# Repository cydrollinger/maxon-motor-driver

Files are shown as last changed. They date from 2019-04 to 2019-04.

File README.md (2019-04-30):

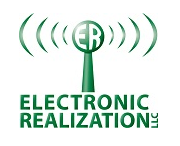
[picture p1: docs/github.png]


>Electronic Realization L.L.C.								   
>Design: Maxon Motor Driver with Bluetooth v4.2/5.0		   
>Engineer: Cy Drollinger								   
>Date: 4/18												           
>Email: cy@elec-real.com
>Website: https://elec-real.com								   
>Address: 2023 Stadium Dr Suite 2B #210 Bozeman, MT 59715				   
>Phone: 406-539-8117	

**NOTE:**
 This case study has been tested and functions as specified. ER is a professional design house and monetary compensation is required for additional work toward this design enabling your monetary success, but conversation is welcome and appreciated toward improving any or all this design and its repository. 

 Think critically while operating and or redesigning this system. Open electronic circuitry can be dangerous due to easily shorting circuits which can generate immediate and intense heat resulting in fire. This is only one example of ill advised use. 			   
	 
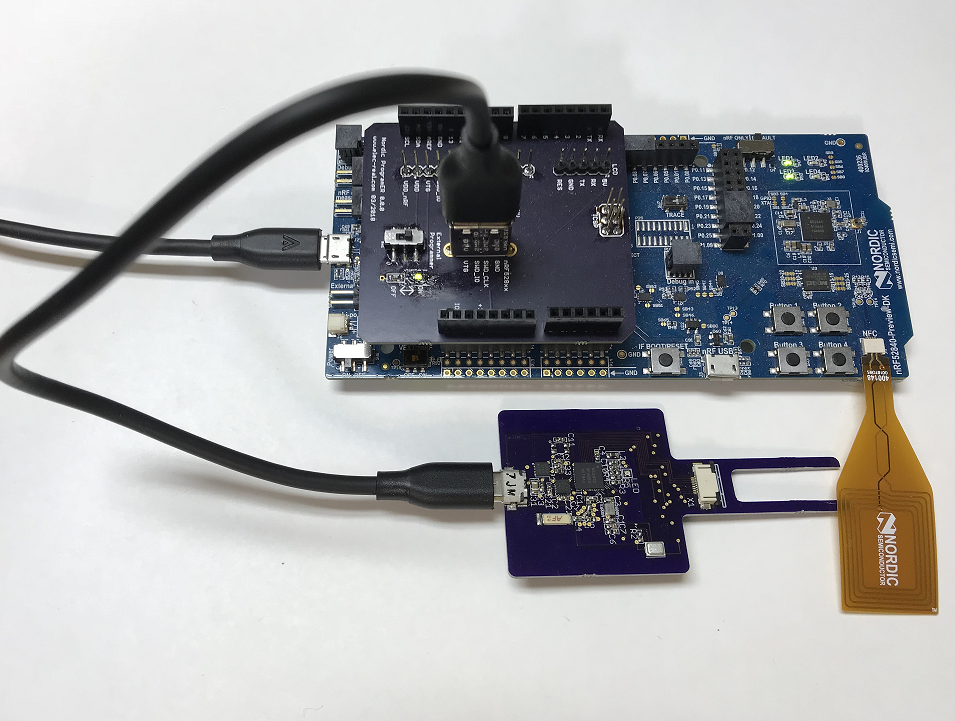
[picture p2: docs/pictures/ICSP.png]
Maxon Motor Driver


**PURPOSE:**
The puspose of this design was to implement a 3 phase DC motor driver for a high speed 8mm dia motor by
Maxon. The system utilizes the nRF52832 by Nordic Semicondutor which outputs bluetooth v4.2/5.0 wireless
communication. The device also boast the mpu9250 a 9 axis inertial sensor as well as a TDK's MEMs micro phone. 

>**File Arcitecture with a terse description**

* FOLDERS:
	* docs		: datasheets charging IC and battery holder
	* hardware	: eagle cadsoft(v7.7) hardware design files 	
		* library		: eagle part files 
		* manufacturing	: files required to produce the design
			* bom	: files created to order the parts	
			* gerber	: files generated to manufacture the board
			* 
	* readme.md	: this file
	
(http://www.youtube.com/watch?v=88ky35AwuC4 "maxon motor driver")

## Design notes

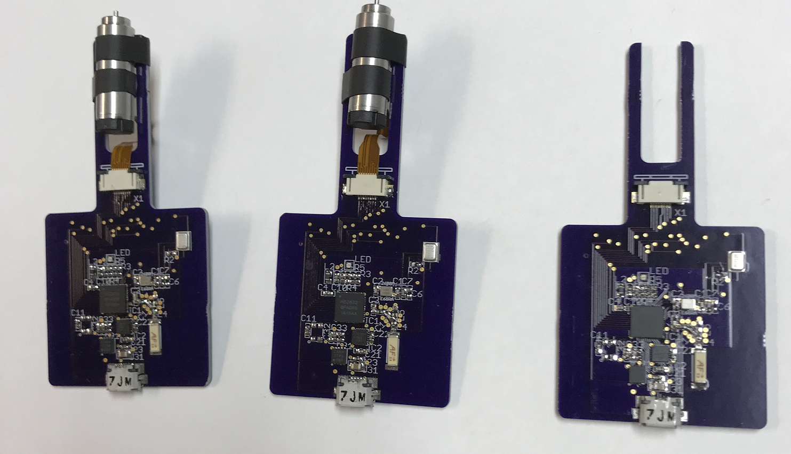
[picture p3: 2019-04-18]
docs/pictures/Max Motor.png

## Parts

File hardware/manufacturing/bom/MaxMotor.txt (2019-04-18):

Partlist exported from C:/Users/Cy/Documents/eagle/Max motor/MaxMotor.sch at 4/23/2018 2:59 PM

Qty Value                       Device                      Package              Parts            Description                                      

1   ANTENNA2SMD5                ANTENNA2SMD5                ANTENNA-CHIP5        U$1              Antenna                                          

CAPACITOR
1   .8pF                        C-ERC0402                   C0402                C3                                                                
1   2.2pF                       C-ERC0402                   C0402                C13                                                               
2   20pF                        C-ERC0402                   C0402                C1, C2                                                            
1   100pF                       C-ERC0402                   C0402                C7                                                                
1   1.0nF                       C-ERC0402                   C0402                C32                                                               
1   10nF                        C-ERC0402                   C0402                C22                                                               
3   100nF                       C-ERC0402                   C0402                C4, C5, C8, C11, C21, C23                                                        
2   1.0uF                       C-ERC0402                   C0402                C10, C33                                                          
2   4.7UF                       C-ER                        C0805                C9, C31                                                               
1                               C-ERC0402                   C0402                C6                                                                

CONNECTOR
1   MICRO-USB-SHIELD-ZX62R-B-5P MICRO-USB-SHIELD-ZX62R-B-5P ZX62R-B-5P           U$4              Hirose Micro USB Connector                       
1   52745-0890                  52745-0890                  52745-0890           X1               FFC/FPC-to-Board  0.50mm (.020") SMT Top Contact 

CRYSTAL
1   FA-128                      FA-128                      FA-128               16M                                                               

IC
1   NRF52832                    NRF52832                    QFN48                IC1                                                               
1   MPU9250_CORRECTED           MPU9250_CORRECTED           3X3_24_QFN_CORRECTED IC2                                                               
1   MCP1727                     MCP1727                     DFN8-3X3             IC3                                                               
1   TSL238T                     TSL238T                     T4                   IC4                                                               
2   ICS-43432                   Microphone                  ICS-43432            IC5, IC6

INDUCTOR
2   3.9nH                       L-ERL402                    R0402                L1, L4                                                            
1   15nH                        L-ERL402                    R0402                L3                                                                
1   10UH                        L-ERL603                    R0603                L2                                                                
1   N.C.                        L-ERL402                    R0402                L5                                                                

LED
1   1X1RGB                      1X1RGB                      1X1                  LED                                                               

RESISTOR
1   0                           R-ER-TINYR402               R0402                R1                                                                
4   100                         R-ER-TINYR402               R0402                R3, R4, R5, R31                                                   
1   100k                        R-ERR0402                   R0402                R2                                                                

TRANSISTOR
3   FDC2512                     FDC2512                     SSOT6                MD12, MD22, MD32                                                  
3   NCP45524/25                 NCP45524/25                 DFN8                 U$2, U$5, U$6

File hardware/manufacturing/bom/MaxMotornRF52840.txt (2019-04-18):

Partlist exported from C:/Users/Cy/Documents/eagle/Max motor/MaxMotornRF52840.sch at 2/5/2019 1:46 PM

Qty Value        Device                      Package              Parts                  Description                                      DIGIKEY     
ANTENNA
1   ANTENNA2SMD5 ANTENNA2SMD5                ANTENNA-CHIP5        ANT1                   Antenna                                                      

CAPACITORS
2   1.0pF        C-ER201                     C0201                C3, C4                                                                              
2   12pF         C-ER201                     C0201                C1, C2                                                                              
2   20pF         C-ER201                     C0201                C17, C18                                                                            
1   100pF        C-ER201                     C0201                C5                                                                                  
1   820pF        C-ER201                     C0201                C9                                                                                  
2   1.0nF        C-ER201                     C0201                C32, C72                                                                            
4   100nF        C-ER201                     C0201                C7, C8, C10, C12                                                                    
4   1.0uF        C-ER201                     C0201                C33, C73, C14, C15                                                                            
6   4.7uF        C-ERC0402                   C0402                C6, C19, C20, C25,C31, C71                                                                   
3   N.C.         C-ER201                     C0201                C13, C16, C24                                                                       
3                C-ER201                     C0201                C21, C22, C23                                                                       

CLOCK
1   ABM12        ABM12                       ABM12                X2                                                                      SER3800CT-ND
1   ECX32        ECX32                       ECX39                X3                                                                                  

CONNECTOR
1   52745-0890   52745-0890                  52745-0890           X1                     FFC/FPC-to-Board  0.50mm (.020") SMT Top Contact             
1   usb          MICRO-USB-SHIELD-ZX62R-B-5P ZX62R-B-5P           USB/SWD                Hirose Micro USB Connector                                   

DIODE
1                DIODE-SOD123                SOD123               D1                     DIODE                                                        

INDUCTOR
1   3.9nH        L-ER0201                    C0201@1              L1                                                                                  

INTEGRATED CIRCUIT
1   NRF52840     NRF52840                    AQFN73               IC1                                                                                 
1   ICM20948     ICM20948                    3X3_24_QFN_CORRECTED IC2                                                                                 
2   MCP1727      MCP1727                     DFN8-3X3             IC3, IC7                                                                            
2   ICS-43432    ICS-43432                   ICS-43432            IC5, IC6                                                                            

LED
1   1X1RGB       1X1RGB                      1X1                  LED                                                                                 

RSISTOR
1   0            R-ER-TINY                   R0805                R1                                                                                  
4   0            R-ER0201                    R0201                R6, R7, R8, R9                                                                      
5   100          R-ER0201                    R0201                R3, R4, R5, R31, R71                                                                
3   10k          R-ER0201                    R0201                R10, R11, R12                                                                       
1   100k         R-ER0201                    R0201                R2                                                                                  

TRANSISTOR
6   DMN2320      DMN2320                     AP02002              M1, M2, M3, M4, M5, M6                                                              
3   NCP45524/25  NCP45524/25                 DFN8                 M7, M8, M9

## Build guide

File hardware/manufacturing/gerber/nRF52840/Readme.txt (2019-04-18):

TOP LAYER
top.GTL
topsilk.GTO
topstop.GTS
toppaste.gtp

SECOND LAYER
layer2.G2L

THIRD LAYER
layer3.G3L

BOTTOM LAYER
botsilk.GBO
botstop.GBS
bottom.GBL
botpaste.gbp

HOLES
holes.xln

BOARD OUTLINE
board_ouline.GKO 		//approximately 1.5" x 3.0" 

INSTRUCTIONS
The microstrip is based on calculations from High-Speed Digital Design pg 430

	height: .0067 in.
	width: .014 in.
	er:    3.66
        thickness: .00138

Color: mask Blue silk Yellow

Surface finish: ENEPIG
Board thickness standard ~0.063"

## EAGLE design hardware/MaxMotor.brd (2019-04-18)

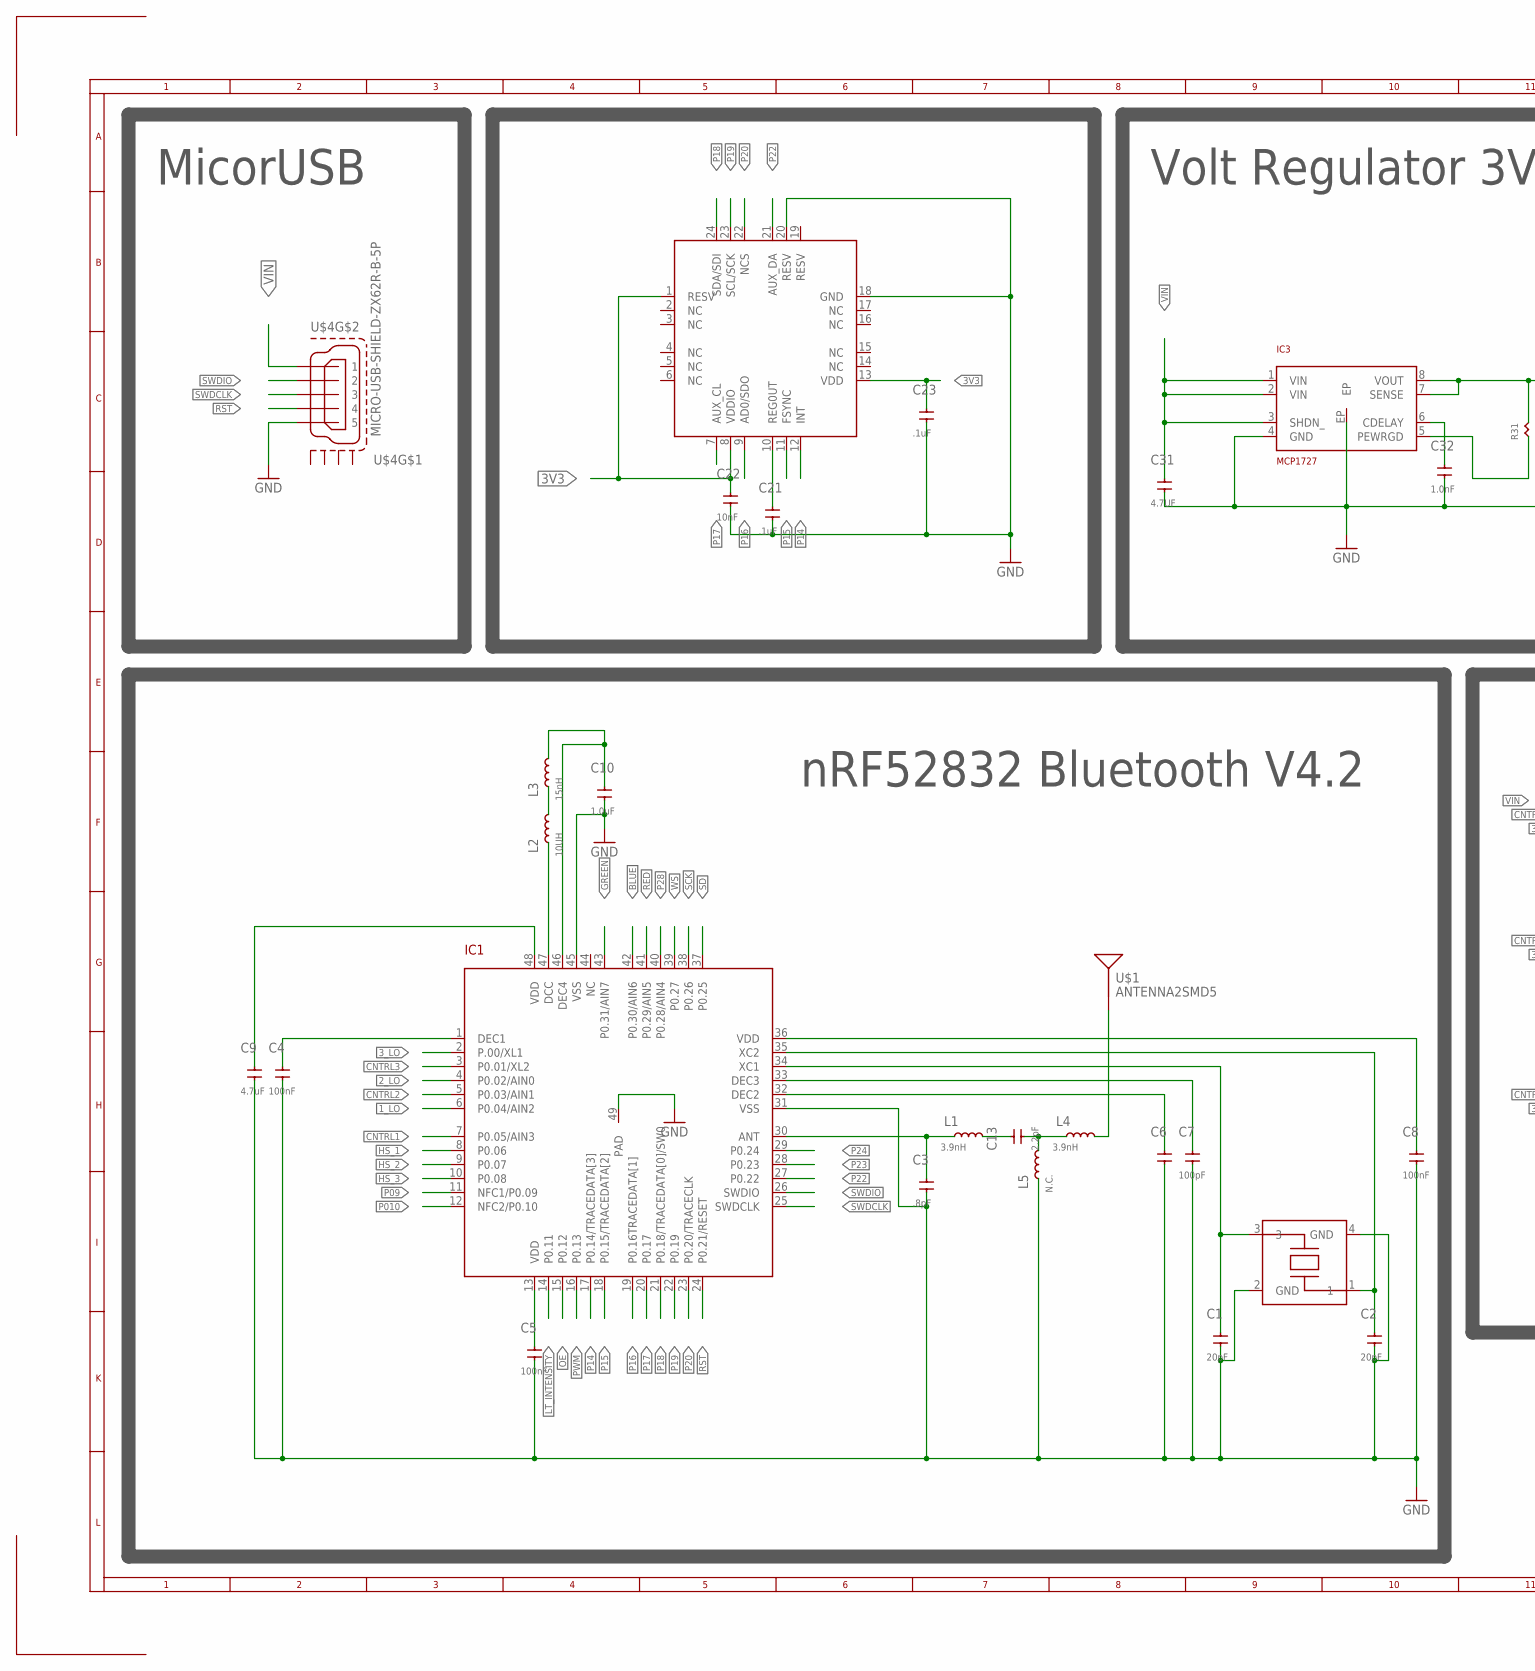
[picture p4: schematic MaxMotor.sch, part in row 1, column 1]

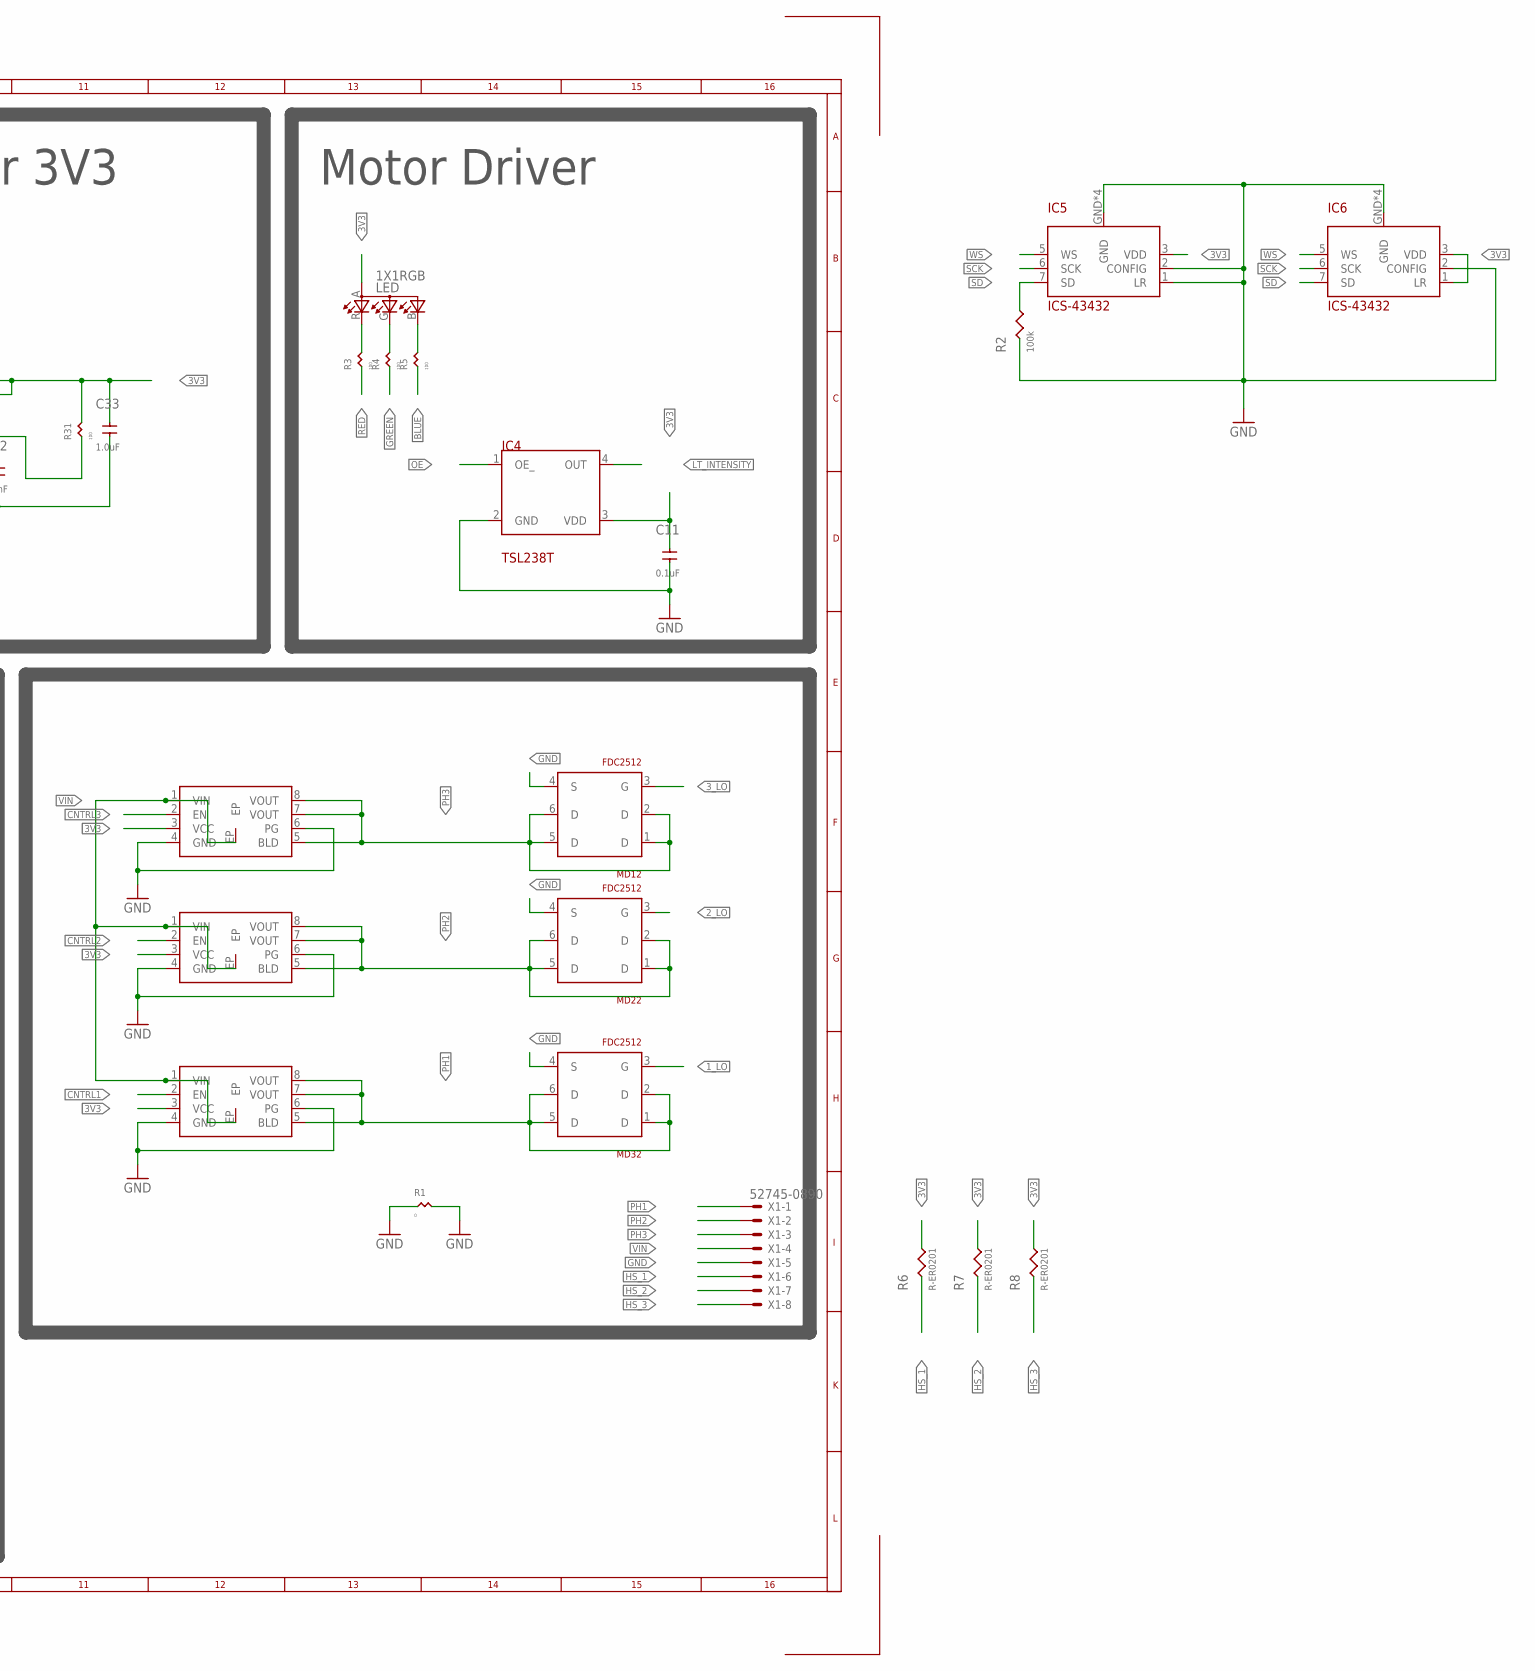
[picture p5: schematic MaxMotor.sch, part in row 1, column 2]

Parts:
C1, C2: 20pF; C0402
C3: .8pF; C0402
C4, C5, C8: 100nF; C0402
C6: C-ERC0402; C0402
C7: 100pF; C0402
C9: 4.7uF; C0805
C10, C33: 1.0uF; C0402
C11: 0.1uF; C0402
C13: 2.2pF; C0402
C21, C23: .1uF; C0402
C22: 10nF; C0402
C31: 4.7UF; C0805
C32: 1.0nF; C0402
IC1: NRF52832; QFN48
IC2: MPU9250_CORRECTED; 3X3_24_QFN_CORRECTED
IC3: MCP1727; DFN8-3X3
IC4: TSL238T; T4
IC5, IC6: ICS-43432
L1, L4: 3.9nH; R0402
L2: 10UH; R0603
L3: 15nH; R0402
L5: N.C.; R0402
LED: 1X1RGB; 1X1
MD12, MD22, MD32: FDC2512; SSOT6
R1: 0; R0402
R2: 100k; R0402
R3, R4, R5, R31: 100; R0402
R6, R7, R8: R-ER0201; R0201
U$1: ANTENNA2SMD5; ANTENNA-CHIP5
U$2, U$5, U$6: NCP45524/25; DFN8
U$4: MICRO-USB-SHIELD-ZX62R-B-5P; ZX62R-B-5P
X1: 52745-0890
XTL16M: FA-128

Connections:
1_LO: IC1.6 (P0.04/AIN2), MD32.3 (G)
2_LO: IC1.4 (P0.02/AIN0), MD22.3 (G)
3V3: C5.2, C8.2, C9.2, C11.2, C22.2, C23.2, C33.2, IC1.13 (VDD), IC1.36 (VDD), IC1.48 (VDD), IC2.1 (RESV), IC2.8 (VDDIO), IC2.13 (VDD), IC3.7 (SENSE), IC3.8 (VOUT), IC4.3 (VDD), IC5.3 (VDD), IC6.1 (LR), IC6.3 (VDD), LED.A (A2), R6.2, R7.2, R8.2, R31.2, U$2.3 (VCC), U$5.3 (VCC), U$6.3 (VCC)
3_LO: IC1.2 (P.00/XL1), MD12.3 (G)
BLUE: IC1.42 (P0.30/AIN6), R5.1
CNTRL1: IC1.7 (P0.05/AIN3), U$6.2 (EN)
CNTRL2: IC1.5 (P0.03/AIN1), U$5.2 (EN)
CNTRL3: IC1.3 (P0.01/XL2), U$2.2 (EN)
GND: C1.1, C2.1, C3.1, C4.1, C5.1, C6.1, C7.1, C8.1, C9.1, C10.1, C11.1, C21.1, C22.1, C23.1, C31.1, C32.1, C33.1, IC1.31 (VSS), IC1.45 (VSS), IC1.49 (PAD), IC2.18 (GND), IC2.20 (RESV), IC3.4 (GND), IC3.EP, IC4.2 (GND), IC5.1 (LR), IC5.2 (CONFIG), IC5.GND, IC5.GND@ (GND), IC5.GND@1 (GND), IC5.GND@2 (GND), IC6.2 (CONFIG), IC6.GND, IC6.GND@ (GND), IC6.GND@1 (GND), IC6.GND@2 (GND), L5.1, MD12.4 (S), MD22.4 (S), MD32.4 (S), R1.1, R1.2, R2.1, U$2.4 (GND), U$2.6 (PG), U$4.1 (5), U$5.4 (GND), U$5.6 (PG), U$6.4 (GND), U$6.6 (PG), X1.5, XTL16M.2 (GND), XTL16M.4 (GND)
GREEN: IC1.43 (P0.31/AIN7), R4.1
HS_1: IC1.8 (P0.06), R6.1, X1.6
HS_2: IC1.9 (P0.07), R7.1, X1.7
HS_3: IC1.10 (P0.08), R8.1, X1.8
LT_INTENSITY: IC1.14 (P0.11), IC4.4 (OUT)
unnamed: C21.2, IC2.10 (REG0UT)
unnamed: C3.2, IC1.30 (ANT), L1.1
unnamed: C6.2, IC1.32 (DEC2)
unnamed: C13.2, L1.2
unnamed: C7.2, IC1.33 (DEC3)
unnamed: C1.2, IC1.34 (XC1), XTL16M.3
unnamed: C2.2, IC1.35 (XC2), XTL16M.1
unnamed: IC1.47 (DCC), L2.1
unnamed: L2.2, L3.1
unnamed: C10.2, IC1.46 (DEC4), L3.2
unnamed: LED.B (CGREEN), R5.2
unnamed: C13.1, L4.1, L5.2
unnamed: L4.2, U$1.FEED
unnamed: LED.G (CBLUE), R4.2
unnamed: IC3.5 (PEWRGD), R31.1
unnamed: LED.R (CRED), R3.2
unnamed: C32.2, IC3.6 (CDELAY)
unnamed: C4.2, IC1.1 (DEC1)
OE: IC1.15 (P0.12), IC4.1 (OE_)
P09: IC1.11 (NFC1/P0.09)
P010: IC1.12 (NFC2/P0.10)
P14: IC1.17 (P0.14/TRACEDATA[3]), IC2.12 (INT)
P15: IC1.18 (P0.15/TRACEDATA[2]), IC2.11 (FSYNC)
P16: IC1.19 (P0.16TRACEDATA[1]), IC2.9 (AD0/SDO)
P17: IC1.20 (P0.17), IC2.7 (AUX_CL)
P18: IC1.21 (P0.18/TRACEDATA[0]/SW0), IC2.24 (SDA/SDI)
P19: IC1.22 (P0.19), IC2.23 (SCL/SCK)
P20: IC1.23 (P0.20/TRACECLK), IC2.22 (NCS)
P22: IC1.27 (P0.22), IC2.21 (AUX_DA)
P23: IC1.28 (P0.23)
P24: IC1.29 (P0.24)
P28: IC1.40 (P0.28/AIN4)
PH1: MD32.1 (D), MD32.2 (D), MD32.5 (D), MD32.6 (D), U$6.5 (BLD), U$6.7 (VOUT), U$6.8 (VOUT), X1.1
PH2: MD22.1 (D), MD22.2 (D), MD22.5 (D), MD22.6 (D), U$5.5 (BLD), U$5.7 (VOUT), U$5.8 (VOUT), X1.2
PH3: MD12.1 (D), MD12.2 (D), MD12.5 (D), MD12.6 (D), U$2.5 (BLD), U$2.7 (VOUT), U$2.8 (VOUT), X1.3
PWM: IC1.16 (P0.13)
RED: IC1.41 (P0.29/AIN5), R3.1
RST: IC1.24 (P0.21/RESET), U$4.2 (4)
SCK: IC1.38 (P0.26), IC5.6 (SCK), IC6.6 (SCK)
SD: IC1.37 (P0.25), IC5.7 (SD), IC6.7 (SD), R2.2
SWDCLK: IC1.25 (SWDCLK), U$4.3
SWDIO: IC1.26 (SWDIO), U$4.4 (2)
VIN: C31.2, IC3.1 (VIN), IC3.2 (VIN), IC3.3 (SHDN_), U$2.1 (VIN), U$2.EP, U$4.5 (1), U$5.1 (VIN), U$5.EP, U$6.1 (VIN), U$6.EP, X1.4
WS: IC1.39 (P0.27), IC5.5 (WS), IC6.5 (WS)

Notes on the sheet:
nRF52832 Bluetooth V4.2
MicorUSB
Volt Regulator 3V3
Motor Driver

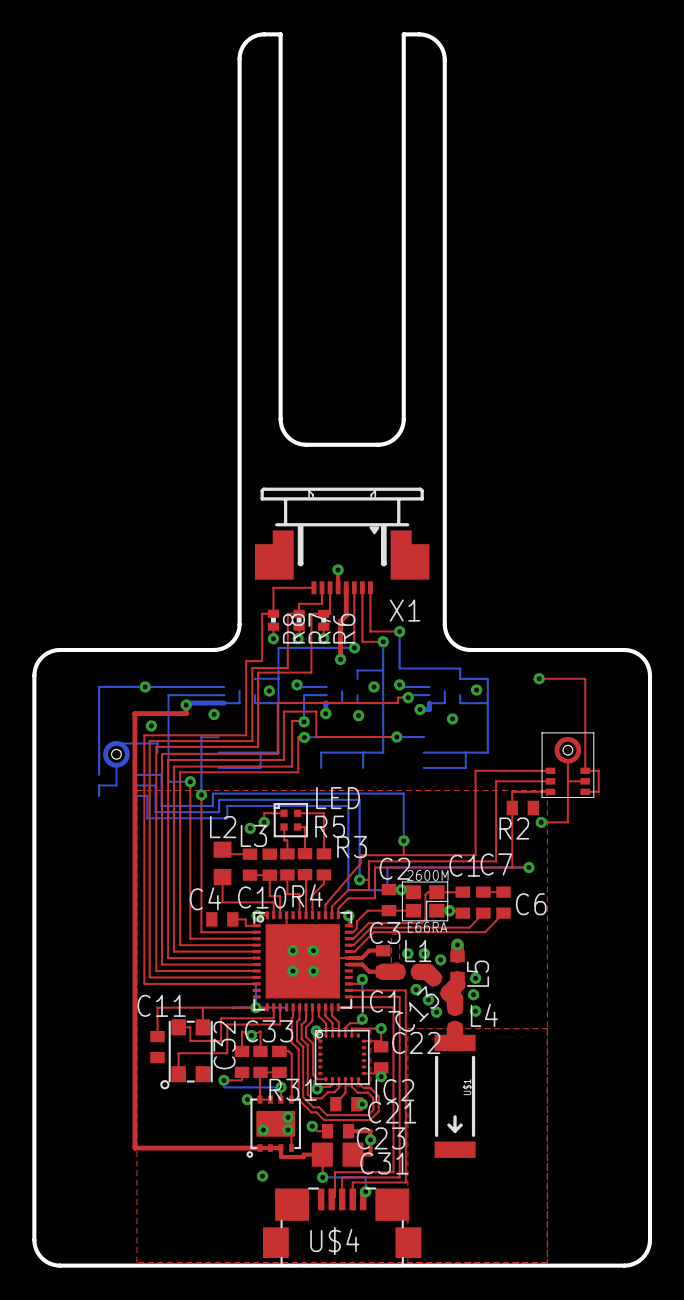
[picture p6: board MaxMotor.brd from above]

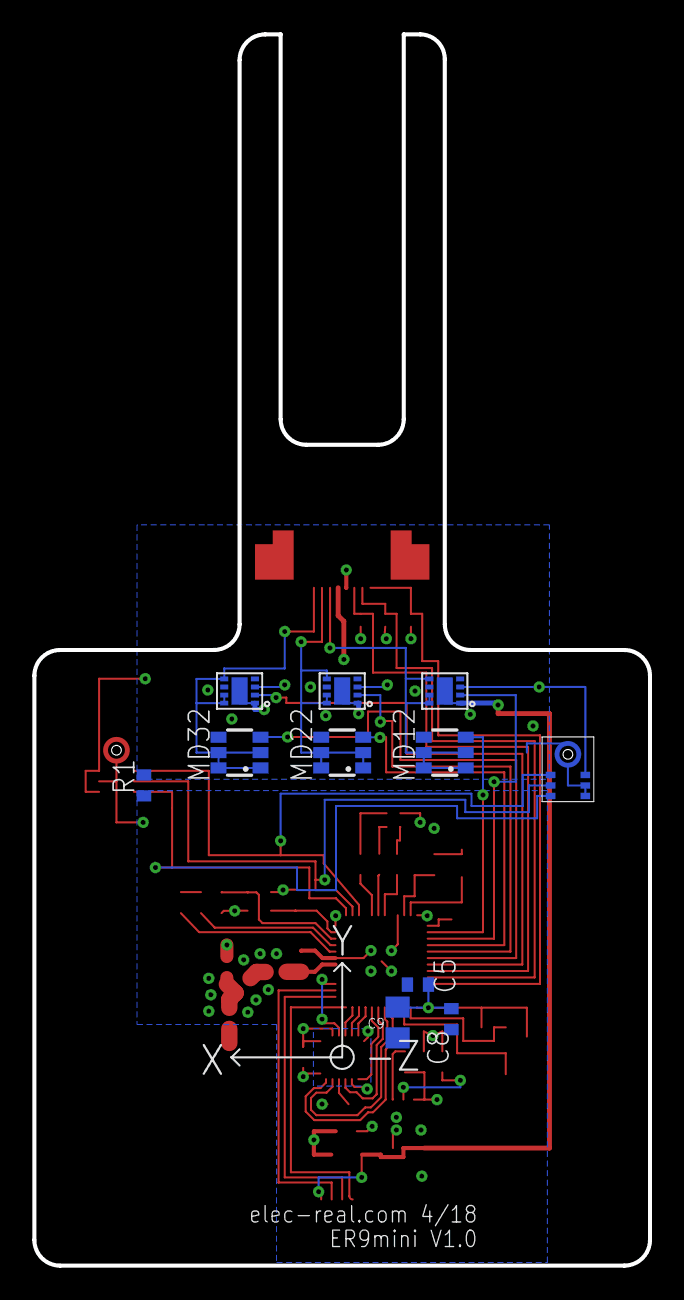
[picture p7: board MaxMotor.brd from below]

Board: 4 copper layers, 38.1 x 76.2 mm, 49 parts (11 on the bottom side), 52 nets.

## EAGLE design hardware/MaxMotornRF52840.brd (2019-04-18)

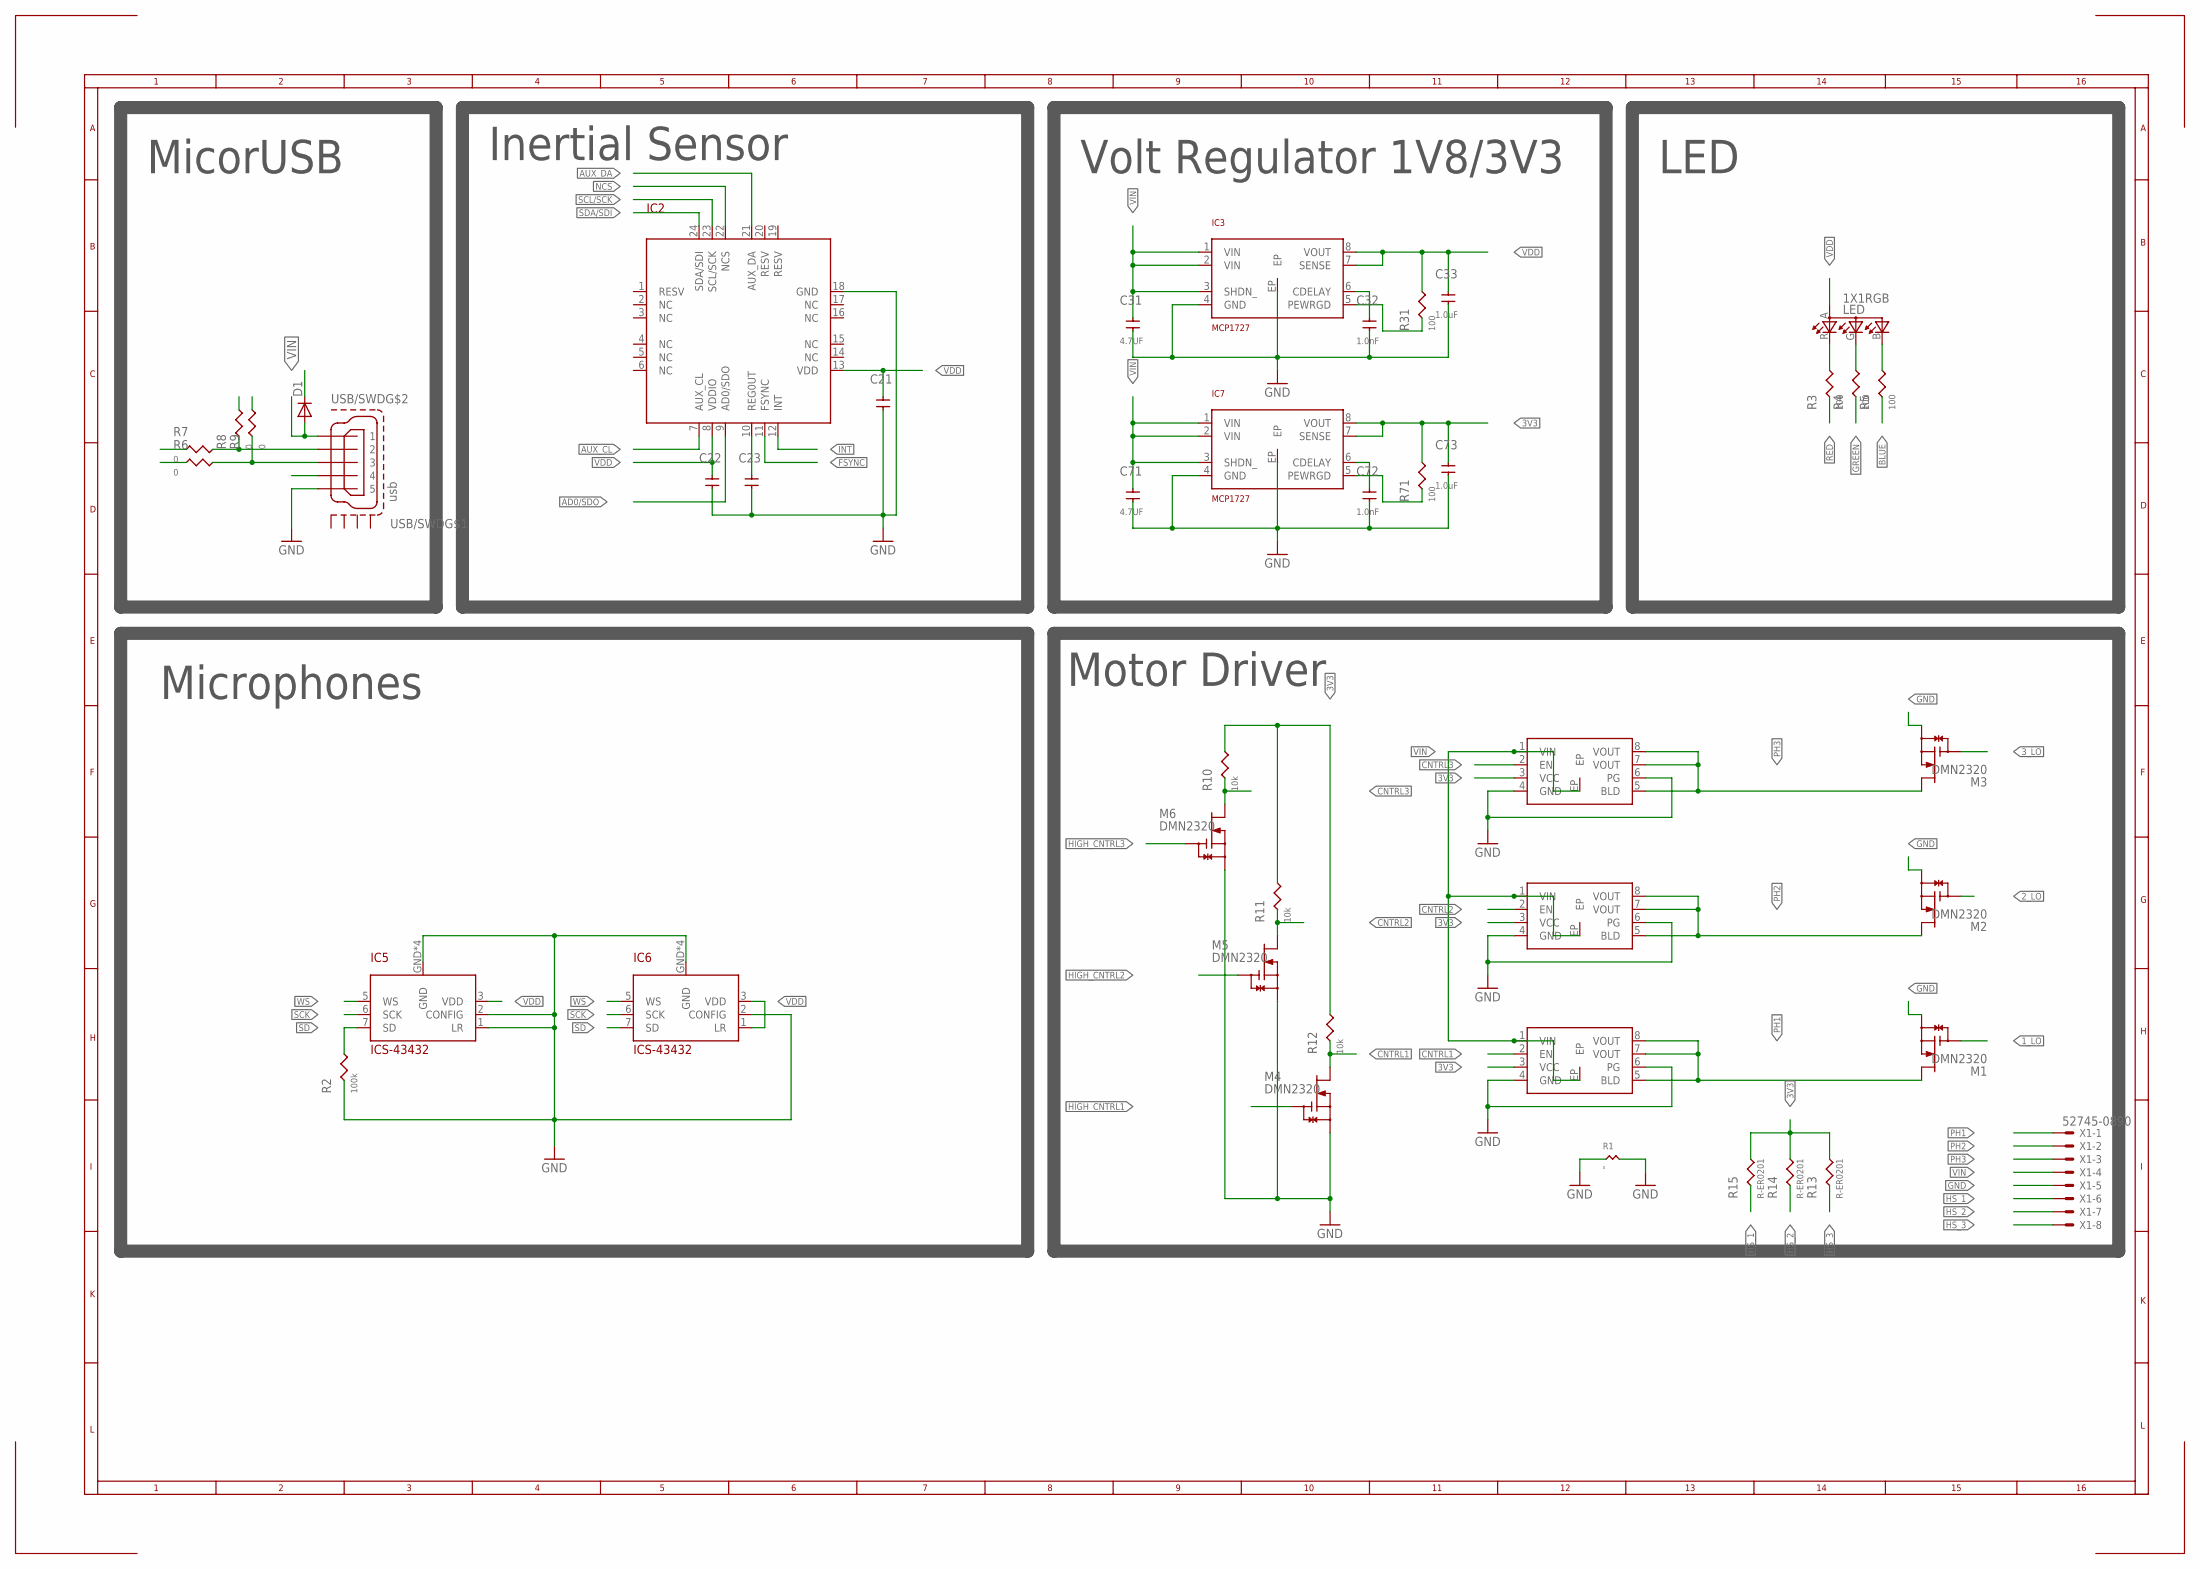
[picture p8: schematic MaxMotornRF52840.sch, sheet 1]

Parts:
C21, C22, C23: C-ER201; C0201
C31, C71: 4.7UF; C0402
C32, C72: 1.0nF; C0201
C33, C73: 1.0uF; C0201
D1: DIODE-SOD123; SOD123
IC2: ICM20948; 3X3_24_QFN_CORRECTED
IC3, IC7: MCP1727; DFN8-3X3
IC5, IC6: ICS-43432
LED: 1X1RGB; 1X1
M1, M2, M3, M4, M5, M6: DMN2320; AP02002
M7, M8, M9: NCP45524/25; DFN8
R1: 0; R0805
R2: 100k; R0201
R3, R4, R5, R31, R71: 100; R0201
R6, R7, R8, R9: 0; R0201
R10, R11, R12: 10k; R0201
R13, R14, R15: R-ER0201; R0201
USB/SWD: usb; ZX62R-B-5P
X1: 52745-0890

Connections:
1_LO: M1.G; also elsewhere on the board
2_LO: M2.G; also elsewhere on the board
3V3: C73.2, IC7.7 (SENSE), IC7.8 (VOUT), M7.3 (VCC), M8.3 (VCC), M9.3 (VCC), R10.2, R11.2, R12.2, R13.2, R14.2, R15.2, R71.2
3_LO: M3.G; also elsewhere on the board
AD0/SDO: IC2.9 (AD0/SDO); also elsewhere on the board
AUX_CL: IC2.7 (AUX_CL)
AUX_DA: IC2.21 (AUX_DA); also elsewhere on the board
BLUE: R5.1; also elsewhere on the board
CNTRL1: M4.D, M7.2 (EN), R12.1
CNTRL2: M5.D, M8.2 (EN), R11.1
CNTRL3: M6.D, M9.2 (EN), R10.1
D+: R6.1; also elsewhere on the board
D-: R7.1; also elsewhere on the board
FSYNC: IC2.11 (FSYNC); also elsewhere on the board
GND: C21.1, C22.1, C23.1, C31.1, C32.1, C33.1, C71.1, C72.1, C73.1, IC2.18 (GND), IC3.4 (GND), IC3.EP, IC5.1 (LR), IC5.2 (CONFIG), IC5.GND, IC5.GND@ (GND), IC5.GND@1 (GND), IC5.GND@2 (GND), IC6.2 (CONFIG), IC6.GND, IC6.GND@ (GND), IC6.GND@1 (GND), IC6.GND@2 (GND), IC7.4 (GND), IC7.EP, M1.S, M2.S, M3.S, M4.S, M5.S, M6.S, M7.4 (GND), M7.6 (PG), M8.4 (GND), M8.6 (PG), M9.4 (GND), M9.6 (PG), R1.1, R1.2, R2.1, USB/SWD.1 (5), X1.5; also elsewhere on the board
GREEN: R4.1; also elsewhere on the board
HIGH_CNTRL1: M4.G; also elsewhere on the board
HIGH_CNTRL2: M5.G; also elsewhere on the board
HIGH_CNTRL3: M6.G; also elsewhere on the board
HS_1: R15.1, X1.6; also elsewhere on the board
HS_2: R14.1, X1.7; also elsewhere on the board
HS_3: R13.1, X1.8; also elsewhere on the board
INT: IC2.12 (INT); also elsewhere on the board
unnamed: C23.2, IC2.10 (REG0UT)
unnamed: IC7.5 (PEWRGD), R71.1
unnamed: C72.2, IC7.6 (CDELAY)
unnamed: LED.B (CGREEN), R5.2
unnamed: LED.G (CBLUE), R4.2
unnamed: IC3.5 (PEWRGD), R31.1
unnamed: LED.R (CRED), R3.2
unnamed: C32.2, IC3.6 (CDELAY)
NCS: IC2.22 (NCS); also elsewhere on the board
PH1: M1.D, M7.5 (BLD), M7.7 (VOUT), M7.8 (VOUT), X1.1
PH2: M2.D, M8.5 (BLD), M8.7 (VOUT), M8.8 (VOUT), X1.2
PH3: M3.D, M9.5 (BLD), M9.7 (VOUT), M9.8 (VOUT), X1.3
RED: R3.1; also elsewhere on the board
SCK: IC5.6 (SCK), IC6.6 (SCK); also elsewhere on the board
SCL/SCK: IC2.23 (SCL/SCK); also elsewhere on the board
SD: IC5.7 (SD), IC6.7 (SD), R2.2; also elsewhere on the board
SDA/SDI: IC2.24 (SDA/SDI); also elsewhere on the board
SWDCLK: R9.2; also elsewhere on the board
SWDIO: R8.2; also elsewhere on the board
USB2: R7.2, R8.1, USB/SWD.4 (2)
USB3: R6.2, R9.1, USB/SWD.3
USB4: USB/SWD.2 (4)
VBUS: D1.C; also elsewhere on the board
VDD: C21.2, C22.2, C33.2, IC2.8 (VDDIO), IC2.13 (VDD), IC3.7 (SENSE), IC3.8 (VOUT), IC5.3 (VDD), IC6.1 (LR), IC6.3 (VDD), LED.A (A2), R31.2; also elsewhere on the board
VIN: C31.2, C71.2, D1.A, IC3.1 (VIN), IC3.2 (VIN), IC3.3 (SHDN_), IC7.1 (VIN), IC7.2 (VIN), IC7.3 (SHDN_), M7.1 (VIN), M7.EP, M8.1 (VIN), M8.EP, M9.1 (VIN), M9.EP, USB/SWD.5 (1), X1.4
WS: IC5.5 (WS), IC6.5 (WS); also elsewhere on the board

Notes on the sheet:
MicorUSB
Volt Regulator 1V8/3V3
LED
Motor Driver
Inertial Sensor
Microphones

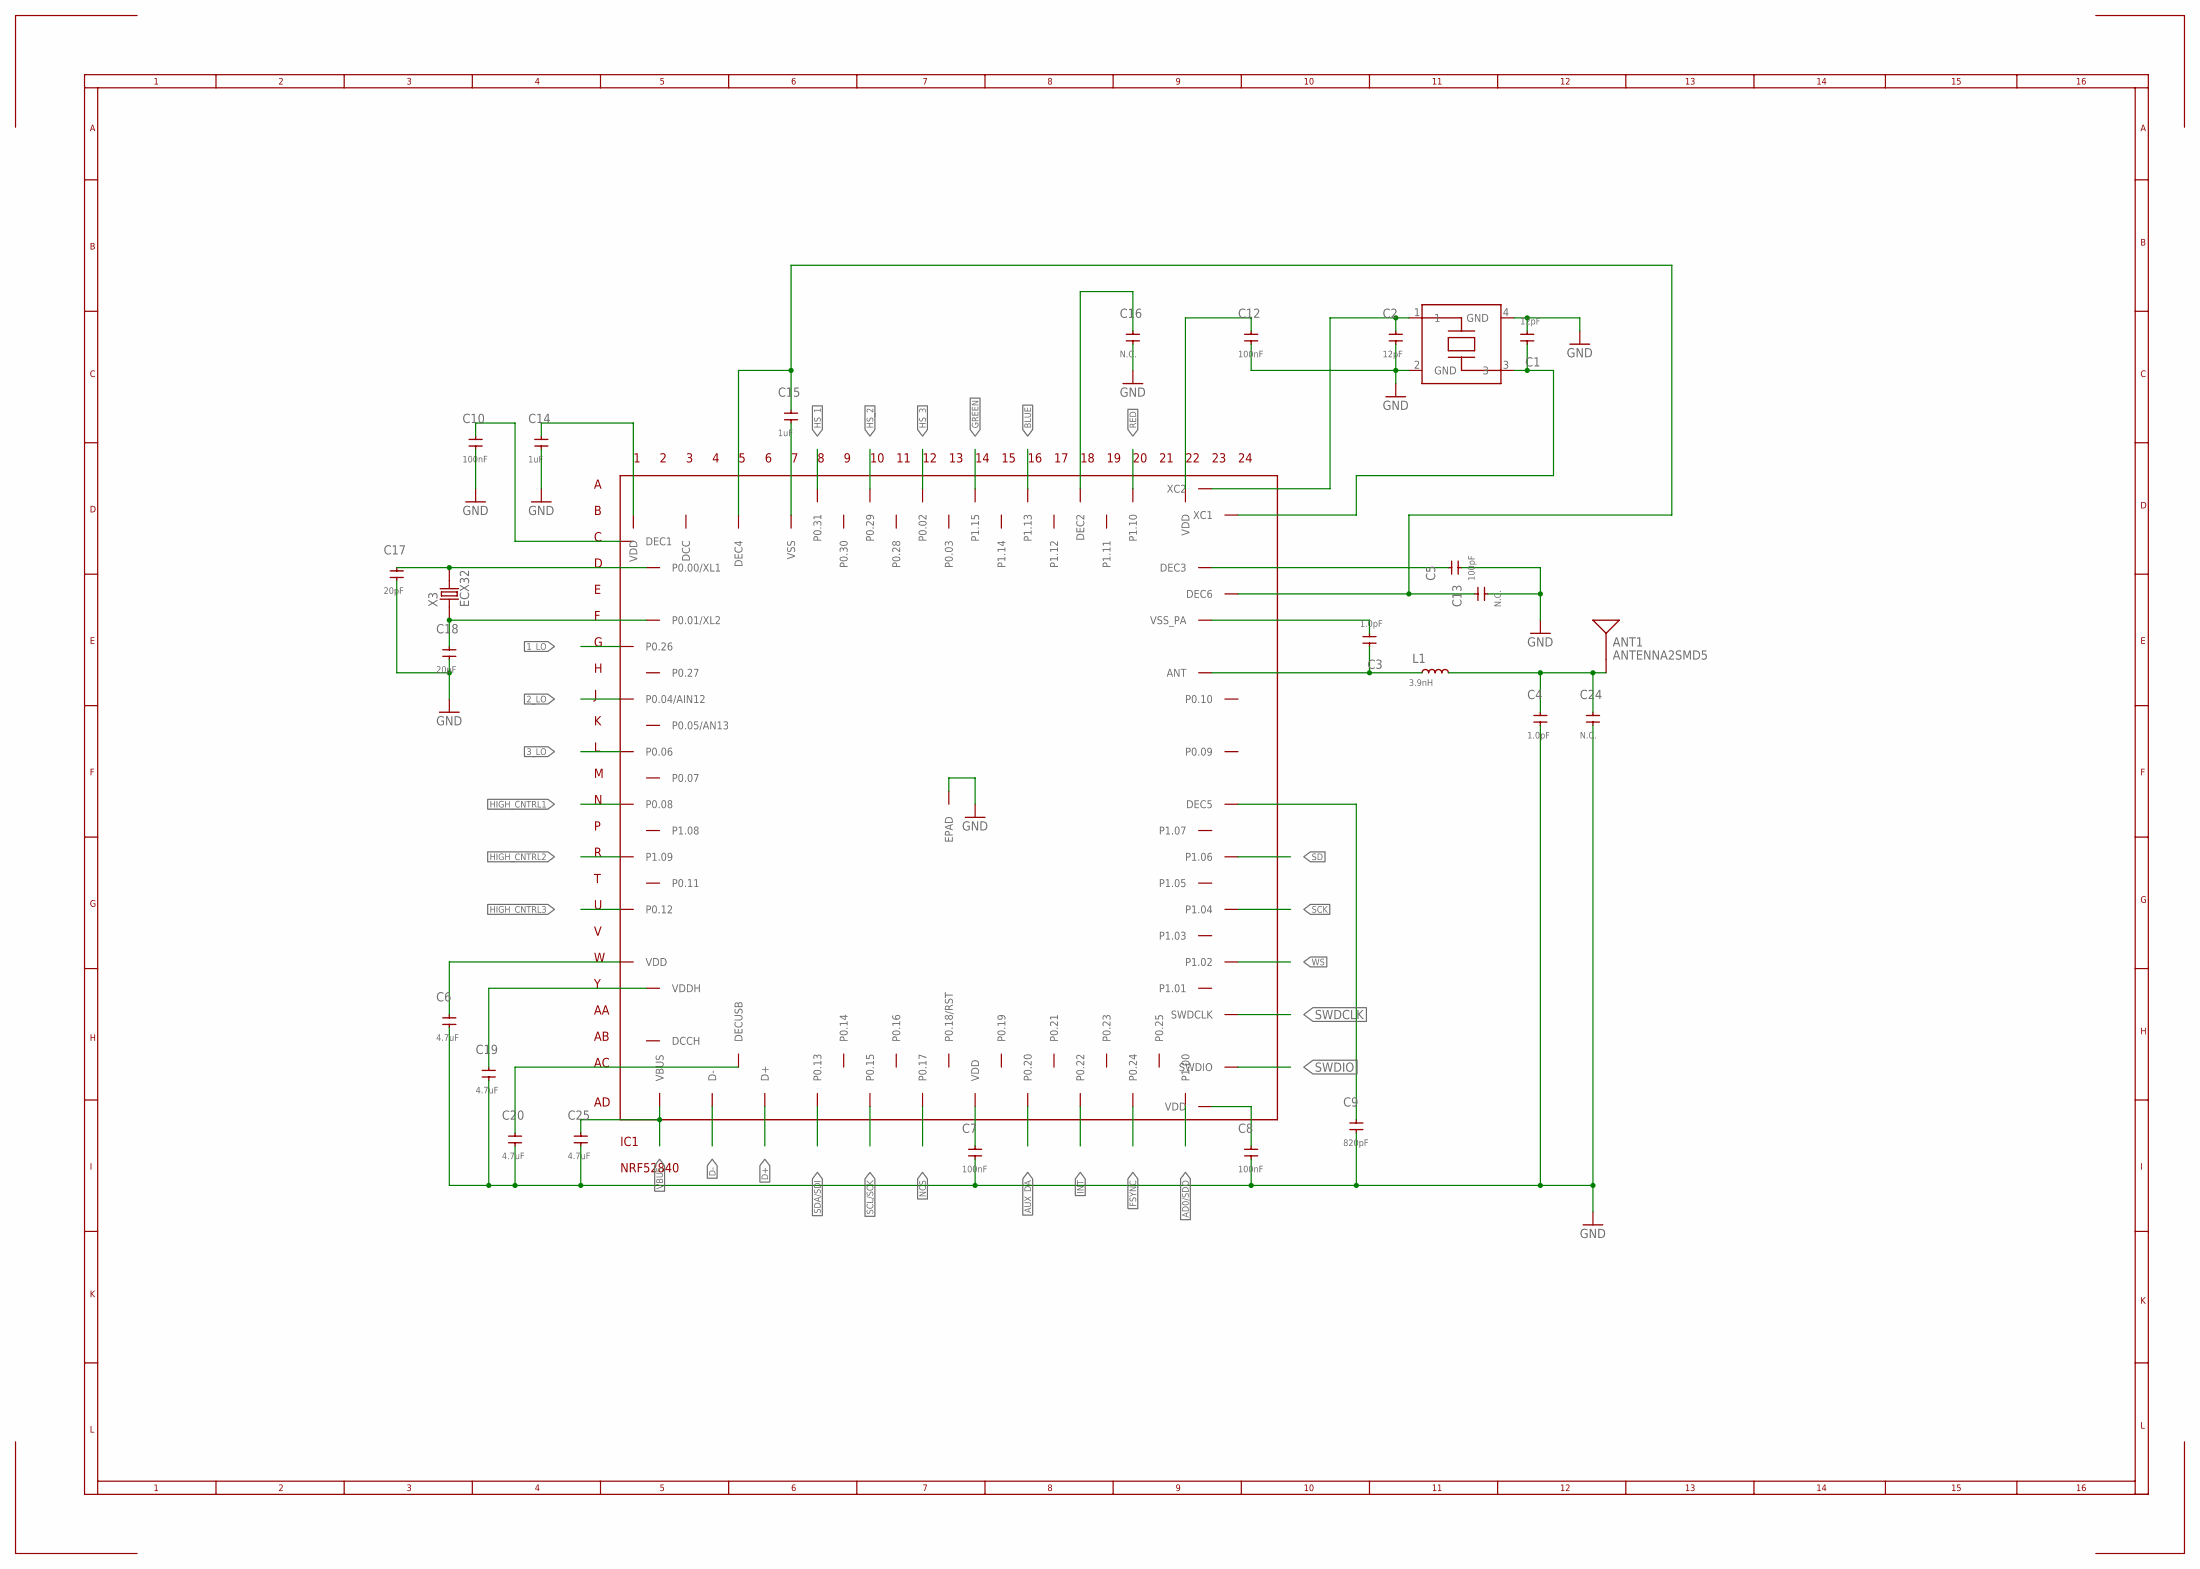
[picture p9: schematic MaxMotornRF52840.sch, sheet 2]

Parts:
ANT1: ANTENNA2SMD5; ANTENNA-CHIP5
C1, C2: 12pF; C0201
C3, C4: 1.0pF; C0201
C5: 100pF; C0201
C6, C19, C20, C25: 4.7uF; C0402
C7, C8, C10, C12: 100nF; C0201
C9: 820pF; C0201
C13, C16, C24: N.C.; C0201
C14, C15: 1uF; C0201
C17, C18: 20pF; C0201
IC1: NRF52840; AQFN73
L1: 3.9nH; C0201@1
X2: ABM12; DIGIKEY SER3800CT-ND
X3: ECX32; ECX39

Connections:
1_LO: IC1.G1 (P0.26); also elsewhere on the board
2_LO: IC1.J1 (P0.04/AIN12); also elsewhere on the board
3_LO: IC1.L1 (P0.06); also elsewhere on the board
AD0/SDO: IC1.AD22 (P1.00); also elsewhere on the board
AUX_DA: IC1.AD16 (P0.20); also elsewhere on the board
BLUE: IC1.A16 (P1.13); also elsewhere on the board
D+: IC1.AD6 (D+); also elsewhere on the board
D-: IC1.AD4 (D-); also elsewhere on the board
FSYNC: IC1.AD20 (P0.24); also elsewhere on the board
GND: C1.1, C2.1, C3.1, C4.1, C5.1, C6.1, C7.1, C8.1, C9.1, C10.1, C12.1, C13.1, C14.1, C15.1, C16.1, C17.1, C18.1, C19.1, C20.1, C24.1, C25.1, IC1.B7 (VSS), IC1.EPAD, IC1.F23 (VSS_PA), X2.2 (GND), X2.4 (GND); also elsewhere on the board
GREEN: IC1.A14 (P1.15); also elsewhere on the board
HIGH_CNTRL1: IC1.N1 (P0.08); also elsewhere on the board
HIGH_CNTRL2: IC1.R1 (P1.09); also elsewhere on the board
HIGH_CNTRL3: IC1.U1 (P0.12); also elsewhere on the board
HS_1: IC1.A8 (P0.31); also elsewhere on the board
HS_2: IC1.A10 (P0.29); also elsewhere on the board
HS_3: IC1.A12 (P0.02); also elsewhere on the board
INT: IC1.AD18 (P0.22); also elsewhere on the board
unnamed: C20.2, IC1.AC5 (DECUSB)
unnamed: C13.2, C15.2, IC1.B5 (DEC4), IC1.E24 (DEC6)
unnamed: C17.2, IC1.D2 (P0.00/XL1), X3.P$2 (2)
unnamed: C16.2, IC1.A18 (DEC2)
unnamed: C3.2, IC1.H23 (ANT), L1.1
unnamed: ANT1.FEED, C4.2, C24.2, L1.2
unnamed: C18.2, IC1.F2 (P0.01/XL2), X3.P$1 (1)
unnamed: C9.2, IC1.N24 (DEC5)
unnamed: C14.2, IC1.B1 (VDD)
unnamed: C5.2, IC1.D23 (DEC3)
NCS: IC1.AD12 (P0.17); also elsewhere on the board
RED: IC1.A20 (P1.10); also elsewhere on the board
SCK: IC1.U24 (P1.04); also elsewhere on the board
SCL/SCK: IC1.AD10 (P0.15); also elsewhere on the board
SD: IC1.R24 (P1.06); also elsewhere on the board
SDA/SDI: IC1.AD8 (P0.13); also elsewhere on the board
SWDCLK: IC1.AA24 (SWDCLK); also elsewhere on the board
SWDIO: IC1.AC24 (SWDIO); also elsewhere on the board
VBUS: C19.2, C25.2, IC1.AD2 (VBUS), IC1.Y2 (VDDH); also elsewhere on the board
VDD: C6.2, C7.2, C8.2, C10.2, C12.2, IC1.A22 (VDD), IC1.AD14 (VDD), IC1.AD23 (VDD), IC1.C1 (DEC1), IC1.W1 (VDD); also elsewhere on the board
WS: IC1.W24 (P1.02); also elsewhere on the board
XC1: C1.2, IC1.B24 (XC1), X2.3
XC2: C2.2, IC1.A23 (XC2), X2.1

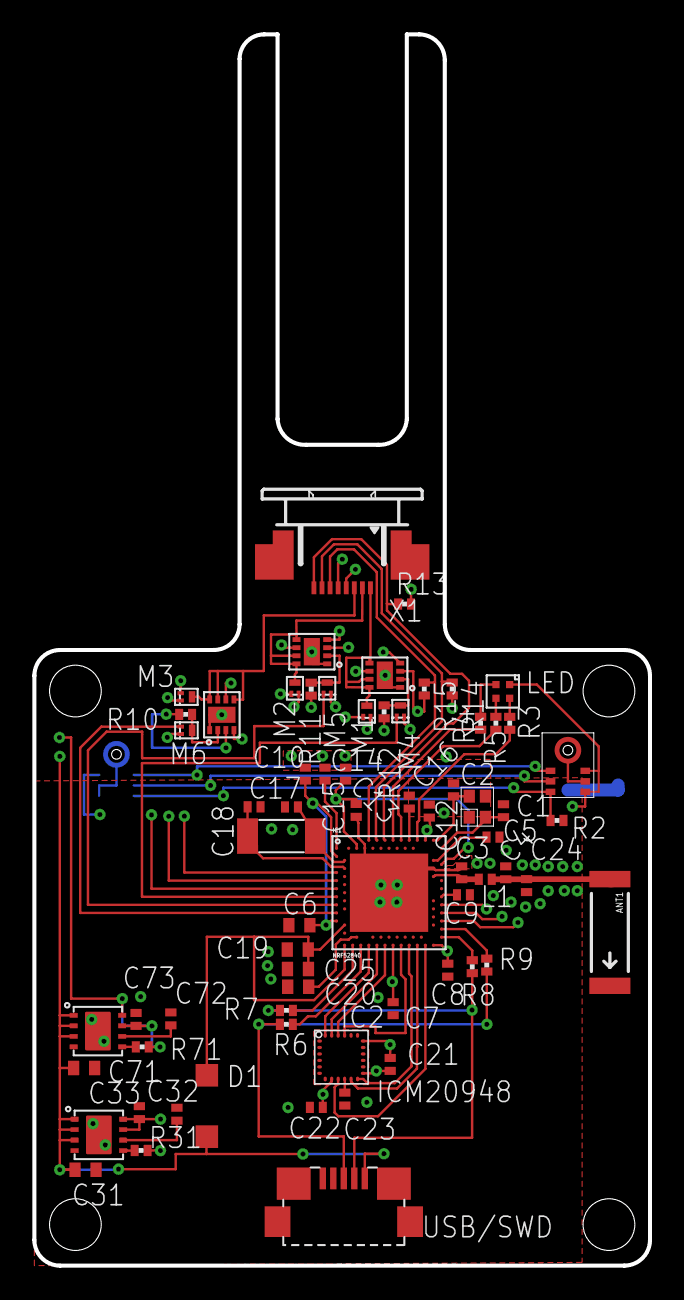
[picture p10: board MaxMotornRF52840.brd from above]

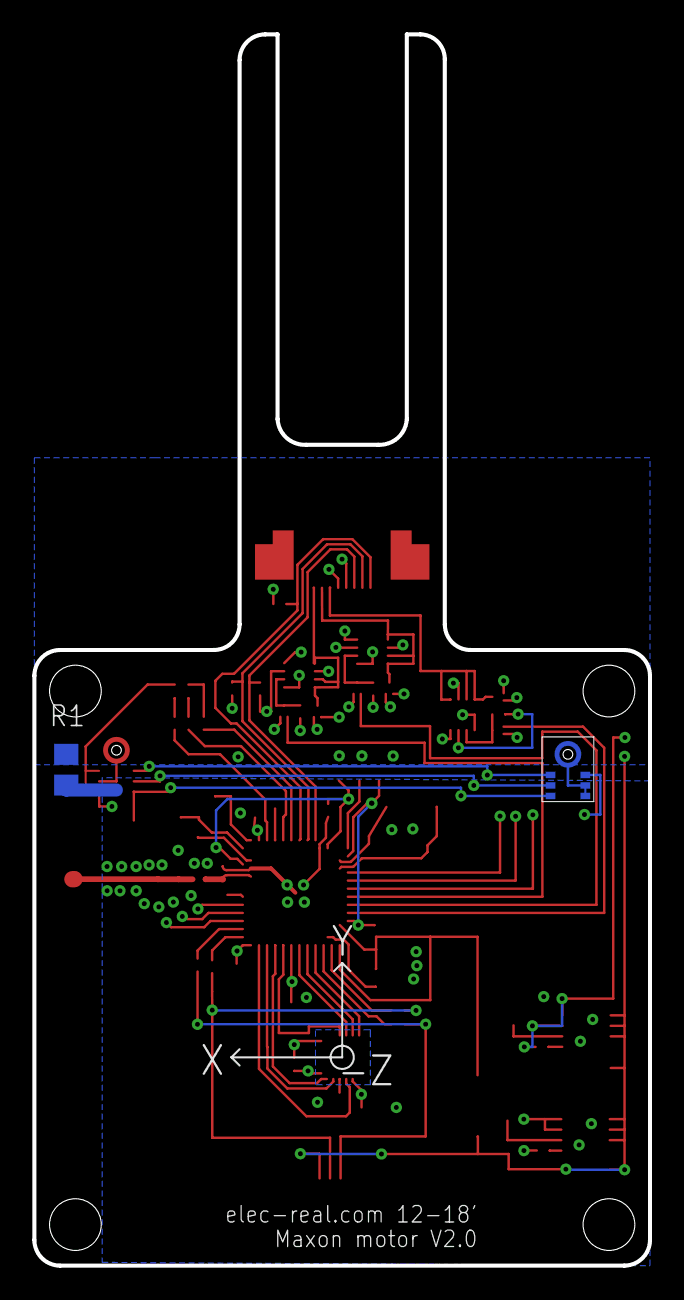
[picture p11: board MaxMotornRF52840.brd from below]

Board: 4 copper layers, 38.1 x 76.2 mm, 70 parts (2 on the bottom side), 59 nets.
